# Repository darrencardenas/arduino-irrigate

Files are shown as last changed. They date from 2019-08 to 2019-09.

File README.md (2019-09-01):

# arduino-irrigate

 ## Introduction
 
 This project contains code, schematics, build plans, and [3D models](https://www.thingiverse.com/thing:3825186) to construct an automated garden watering system.  The main components of the system are an [Arduino Uno Rev3 microcontroller board](https://store.arduino.cc/usa/arduino-uno-rev3), a [soil moisture sensor](https://vegetronix.com/Products/VH400/), and a [water solenoid valve](https://www.adafruit.com/product/997).  The water solenoid valve is connected to a garden hose and a suitable watering device, such as a sprinkler or sprayer.  I used an old garden hose with holes drilled into it.  
 
<p align="center">
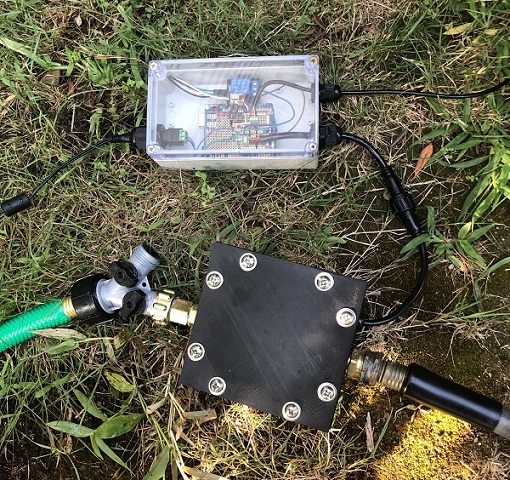
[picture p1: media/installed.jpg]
Installed System

</p>
<p align="center">
Watering Video
</p>   
<br><br>
 
 ## Operation
 At a set time interval, the Arduino checks the moisture sensor for a minimum value. If the reading is below the minimum value, the water valve is opened for a period of time.  The moisture readings are sent via [email](https://www.smtp2go.com/setupguide/arduino/) and [text message](https://www.lifewire.com/sms-gateway-from-email-to-sms-text-message-2495456).  The readings are also saved to a [publicly viewable IoT website](https://community.thingspeak.com/tutorials/arduino/send-data-to-thingspeak-with-arduino/) to store data and generate graphs.

<p align="center">
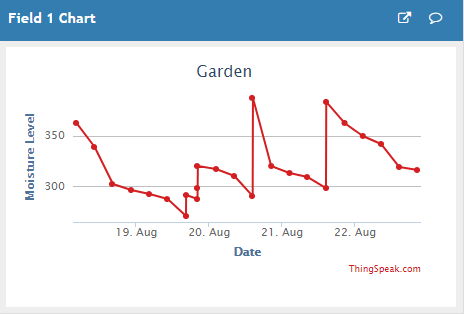
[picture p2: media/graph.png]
Moisture Graph

&nbsp&nbsp&nbsp&nbsp&nbsp&nbsp&nbsp&nbsp&nbsp
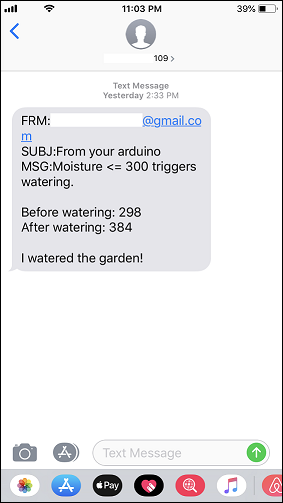
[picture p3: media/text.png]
Text Message

</p>
<br><br>

## Features
- Allows customizable intervals for soil moisture checks and watering
- Leverages waterproof enclosures and cabling
- Sends email and text message (SMS) status updates
- Provides data monitoring via website
- Supports WiFi data transmission using an ESP8266 module
- Powered by a single +12VDC source
<br><br>

<p align="center">
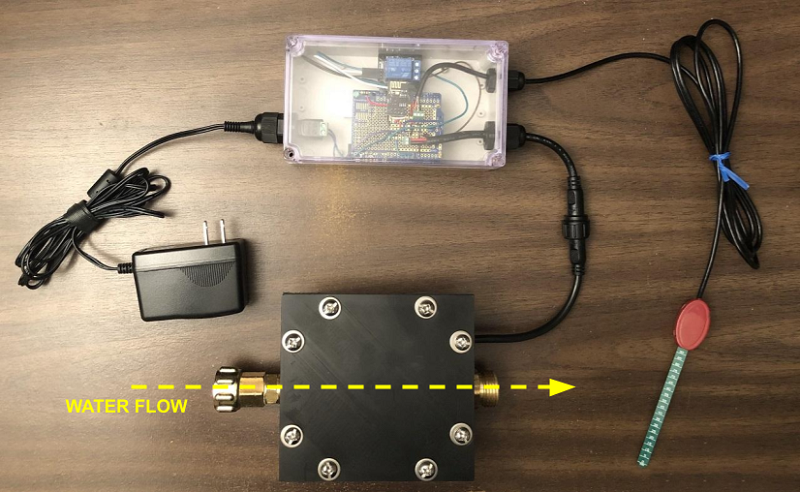
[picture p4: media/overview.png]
Top Down View

</p>
<br><br>

## Schematic Diagram
<p align="center">
<a href="build_plans/schematic_irrigate.pdf">
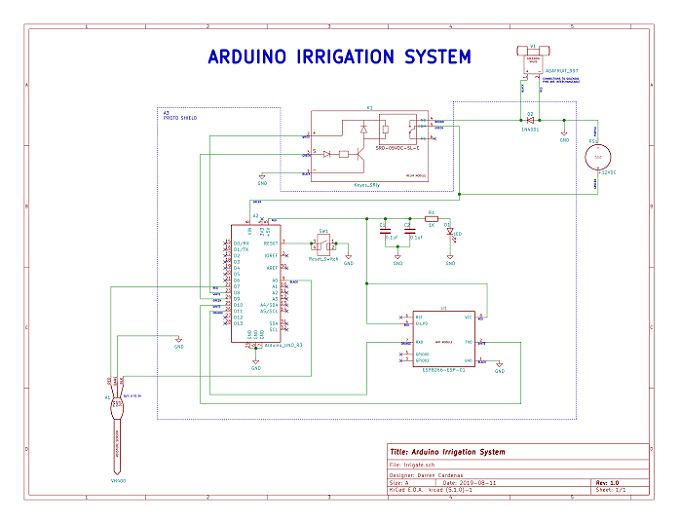
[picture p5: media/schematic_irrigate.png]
</a></p>
<br><br>

## Arduino Code
Developed in Arduino IDE 1.8.9.
<p align="left">
<a href="code/irrigate.ino">
INO file</a></p>
<br><br>

## Arduino Proto Shield Layout
I used screw terminal blocks and a 2x4 female header to allow for easy disassembly.
<p align="center">
<a href="build_plans/shield-layout_irrigate.png">
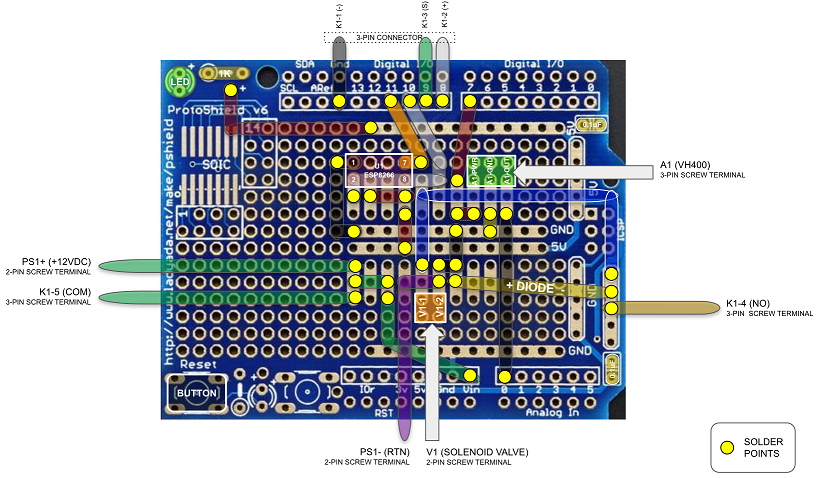
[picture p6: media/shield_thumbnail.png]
</a></p>
<br><br>

## 3D Printed Models
I designed a [custom waterproof enclosure](https://www.thingiverse.com/thing:3825186) to house the water solenoid valve. I used PETG filament and 0.3mm layer height. Enclosure was printed with 10% infill and supports.  Lid was printed with 50% infill and no supports.  I cut a square using gasket material and punched holes for stainless steel screws. 
<p align="center">
<a href="3D_models">
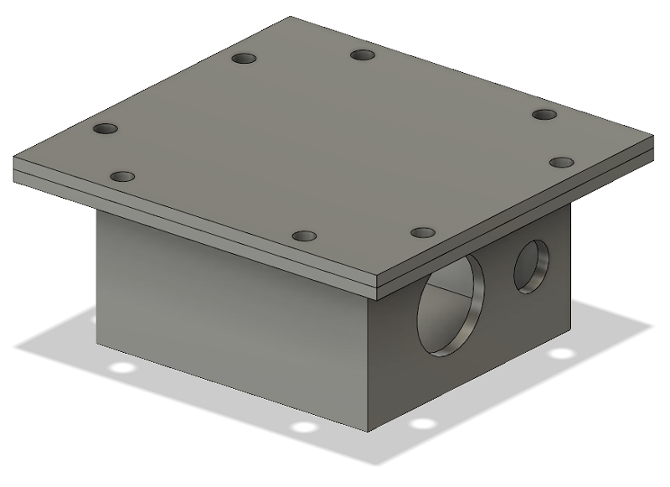
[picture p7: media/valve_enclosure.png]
</a></p>
<br>
<p align="center">
<a href="3D_models/valve_enclosure.stl">
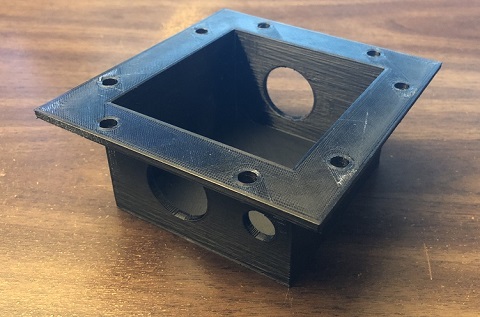
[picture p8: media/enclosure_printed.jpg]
</a>
&nbsp&nbsp
<a href="3D_models/valve_lid.stl">
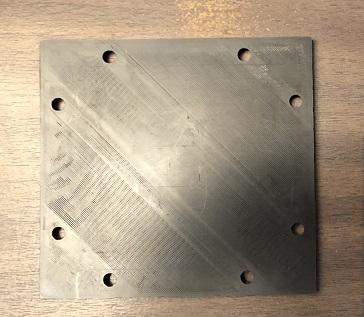
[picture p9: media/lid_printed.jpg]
</a></p>
<br><br>

## Water Solenoid Valve Enclosure 
To install the solenoid valve, insert the bulkhead adapters into the enclosure first.  Then, connect the valve to one of the bulkhead adapters by turning the adapter from outside of the enclosure.  After tightening the first adapter, there should be enough clearance to attach the second adapter.  Then install the bulkhead rubber washers and locknuts. The pipe fittings require teflon tape or thread sealant for leak-proof operation. 
<p align="center">
<a href="build_plans/assembly_valve_enclosure.pdf">
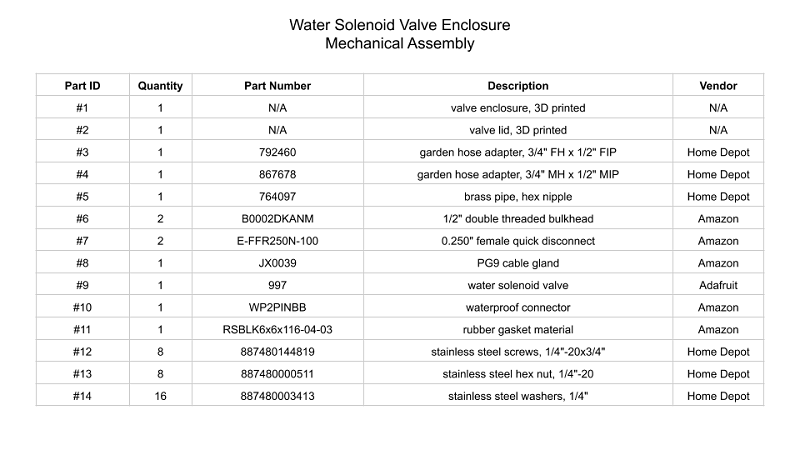
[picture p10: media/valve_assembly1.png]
Valve Assembly 1

</a></p> 
 
<p align="center">
<a href="build_plans/assembly_valve_enclosure.pdf">
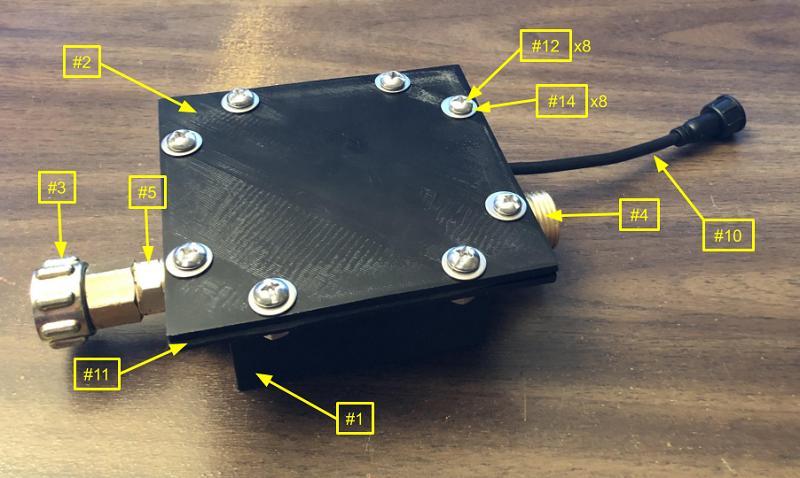
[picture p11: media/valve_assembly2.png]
Valve Assembly 2

</a></p> 

<p align="center">
<a href="build_plans/assembly_valve_enclosure.pdf">
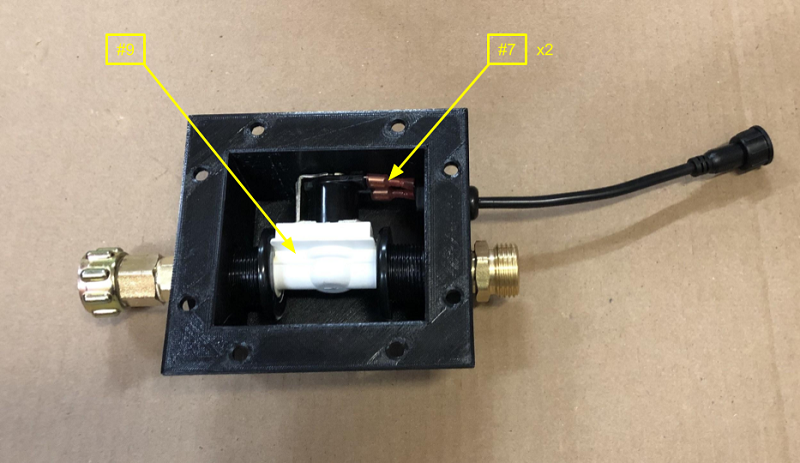
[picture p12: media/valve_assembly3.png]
Valve Assembly 3

</a></p> 

<p align="center">
<a href="build_plans/assembly_valve_enclosure.pdf">
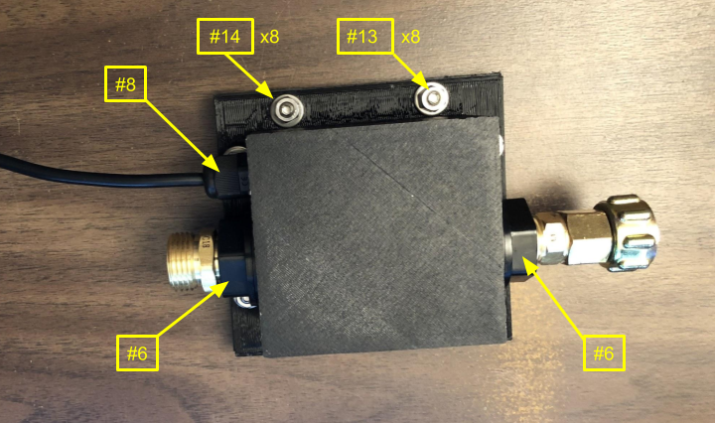
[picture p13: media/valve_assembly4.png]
Valve Assembly 4

</a></p> 
<br><br>

## Arduino Enclosure 
Adafruit provides excellent [instructions](https://learn.adafruit.com/adafruit-proto-shield-arduino?view=all) for the initial set up of the Arduino proto shield.
Install screws and standoffs on the Arduino and relay module. Then use some kind of adhesive to bond the standoffs to the inside of the enclosure.  I used acrylic cement.
<p align="center">
<a href="build_plans/assembly_arduino_enclosure.pdf">
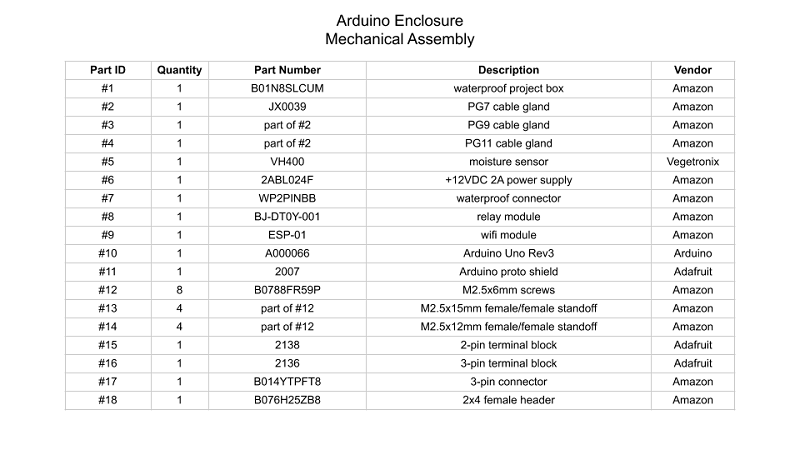
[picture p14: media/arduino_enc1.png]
Arduino Enclosure 1

</a></p> 

<p align="center">
<a href="build_plans/assembly_arduino_enclosure.pdf">
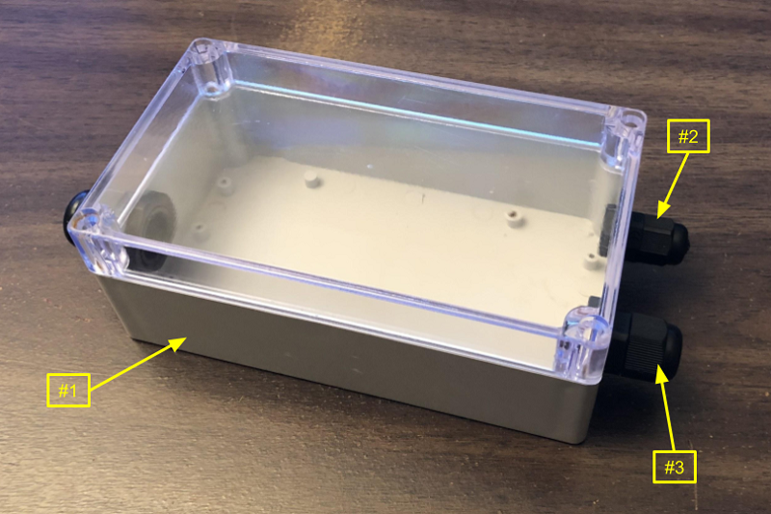
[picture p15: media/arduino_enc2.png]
Arduino Enclosure 2

</a></p> 

<p align="center">
<a href="build_plans/assembly_arduino_enclosure.pdf">
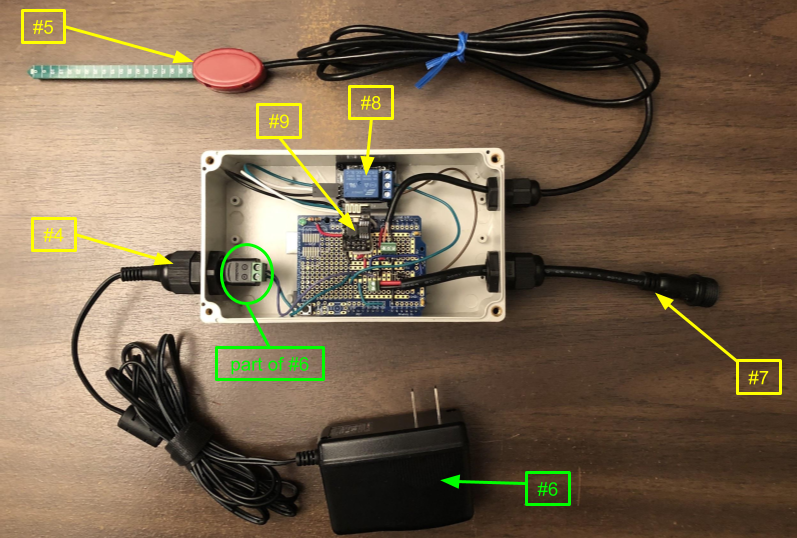
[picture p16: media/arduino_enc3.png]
Arduino Enclosure 3

</a></p> 

<p align="center">
<a href="build_plans/assembly_arduino_enclosure.pdf">
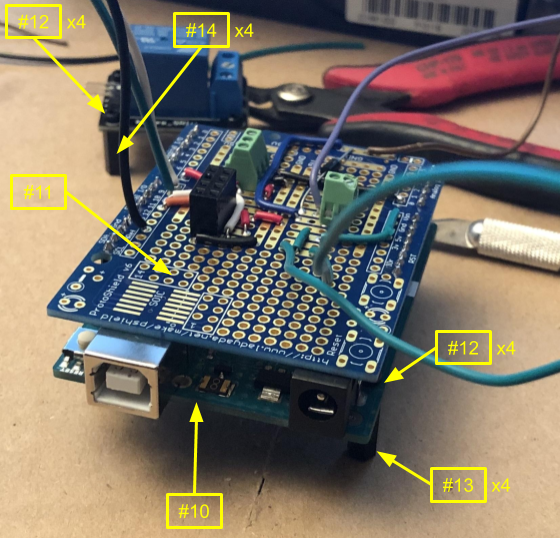
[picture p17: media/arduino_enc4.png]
Arduino Enclosure 4

</a></p> 

<p align="center">
<a href="build_plans/assembly_arduino_enclosure.pdf">
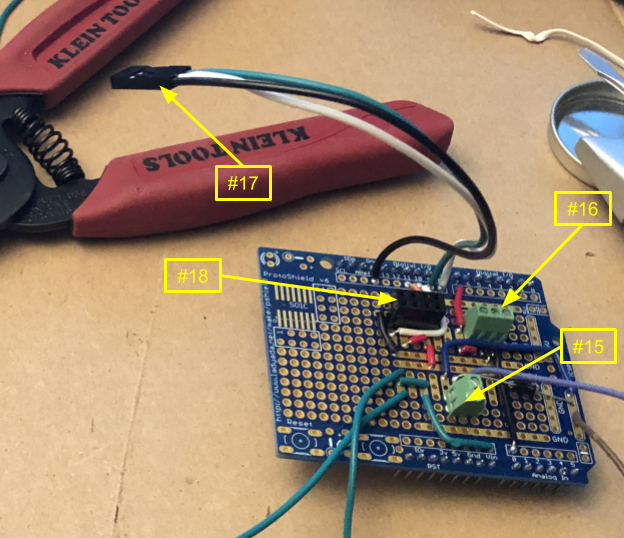
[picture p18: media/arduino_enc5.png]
Arduino Enclosure 5

</a></p> 
<br><br>

## Set Up
- Update the code to include your SSID name/password, [ThingSpeak Write API key](https://community.thingspeak.com/tutorials/arduino/send-data-to-thingspeak-with-arduino/), and [SMTP2GO username/password](https://www.smtp2go.com/setupguide/arduino/).
- Update the email sender and [recipient](https://www.lifewire.com/sms-gateway-from-email-to-sms-text-message-2495456) lists in the code.
- Update the moisture check interval and watering period in the code.
- Update the MOISTURE_MAX value in the code by taking readings with the sensor blade fully submerged in water.
- Update the MOISTURE_THRESHOLD value in the code with your desired value. 
- Ensure water pressure going to the [water solenoid valve](https://www.adafruit.com/product/997) is at least 3PSI.
- The water solenoid valve is uni-directional. Confirm water flow will be in the correct direction.

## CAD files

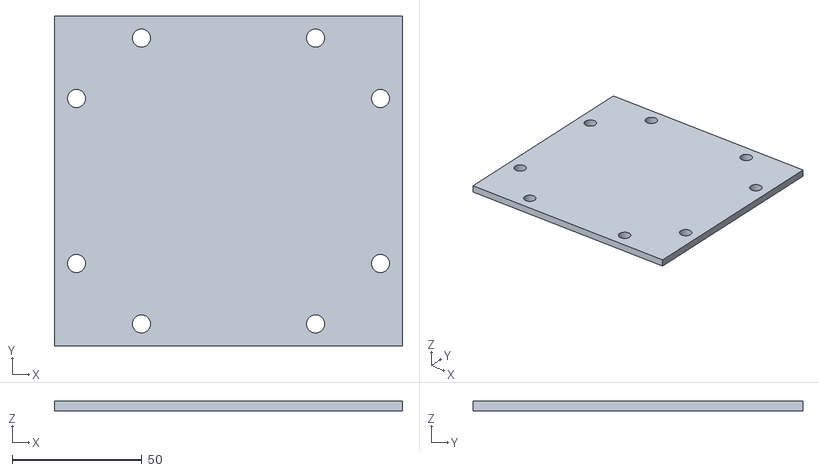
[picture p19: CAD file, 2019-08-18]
3D_models/valve_lid.stl
134.0 x 127.0 x 4.00

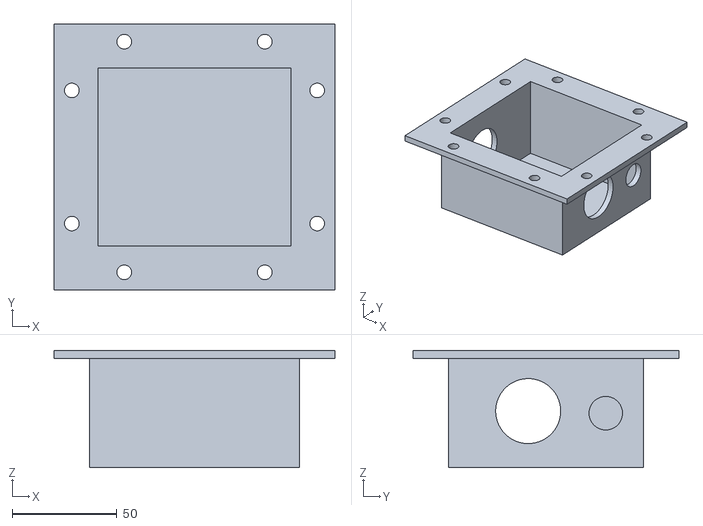
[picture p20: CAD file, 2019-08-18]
3D_models/valve_enclosure.stl
134.0 x 127.0 x 56.0

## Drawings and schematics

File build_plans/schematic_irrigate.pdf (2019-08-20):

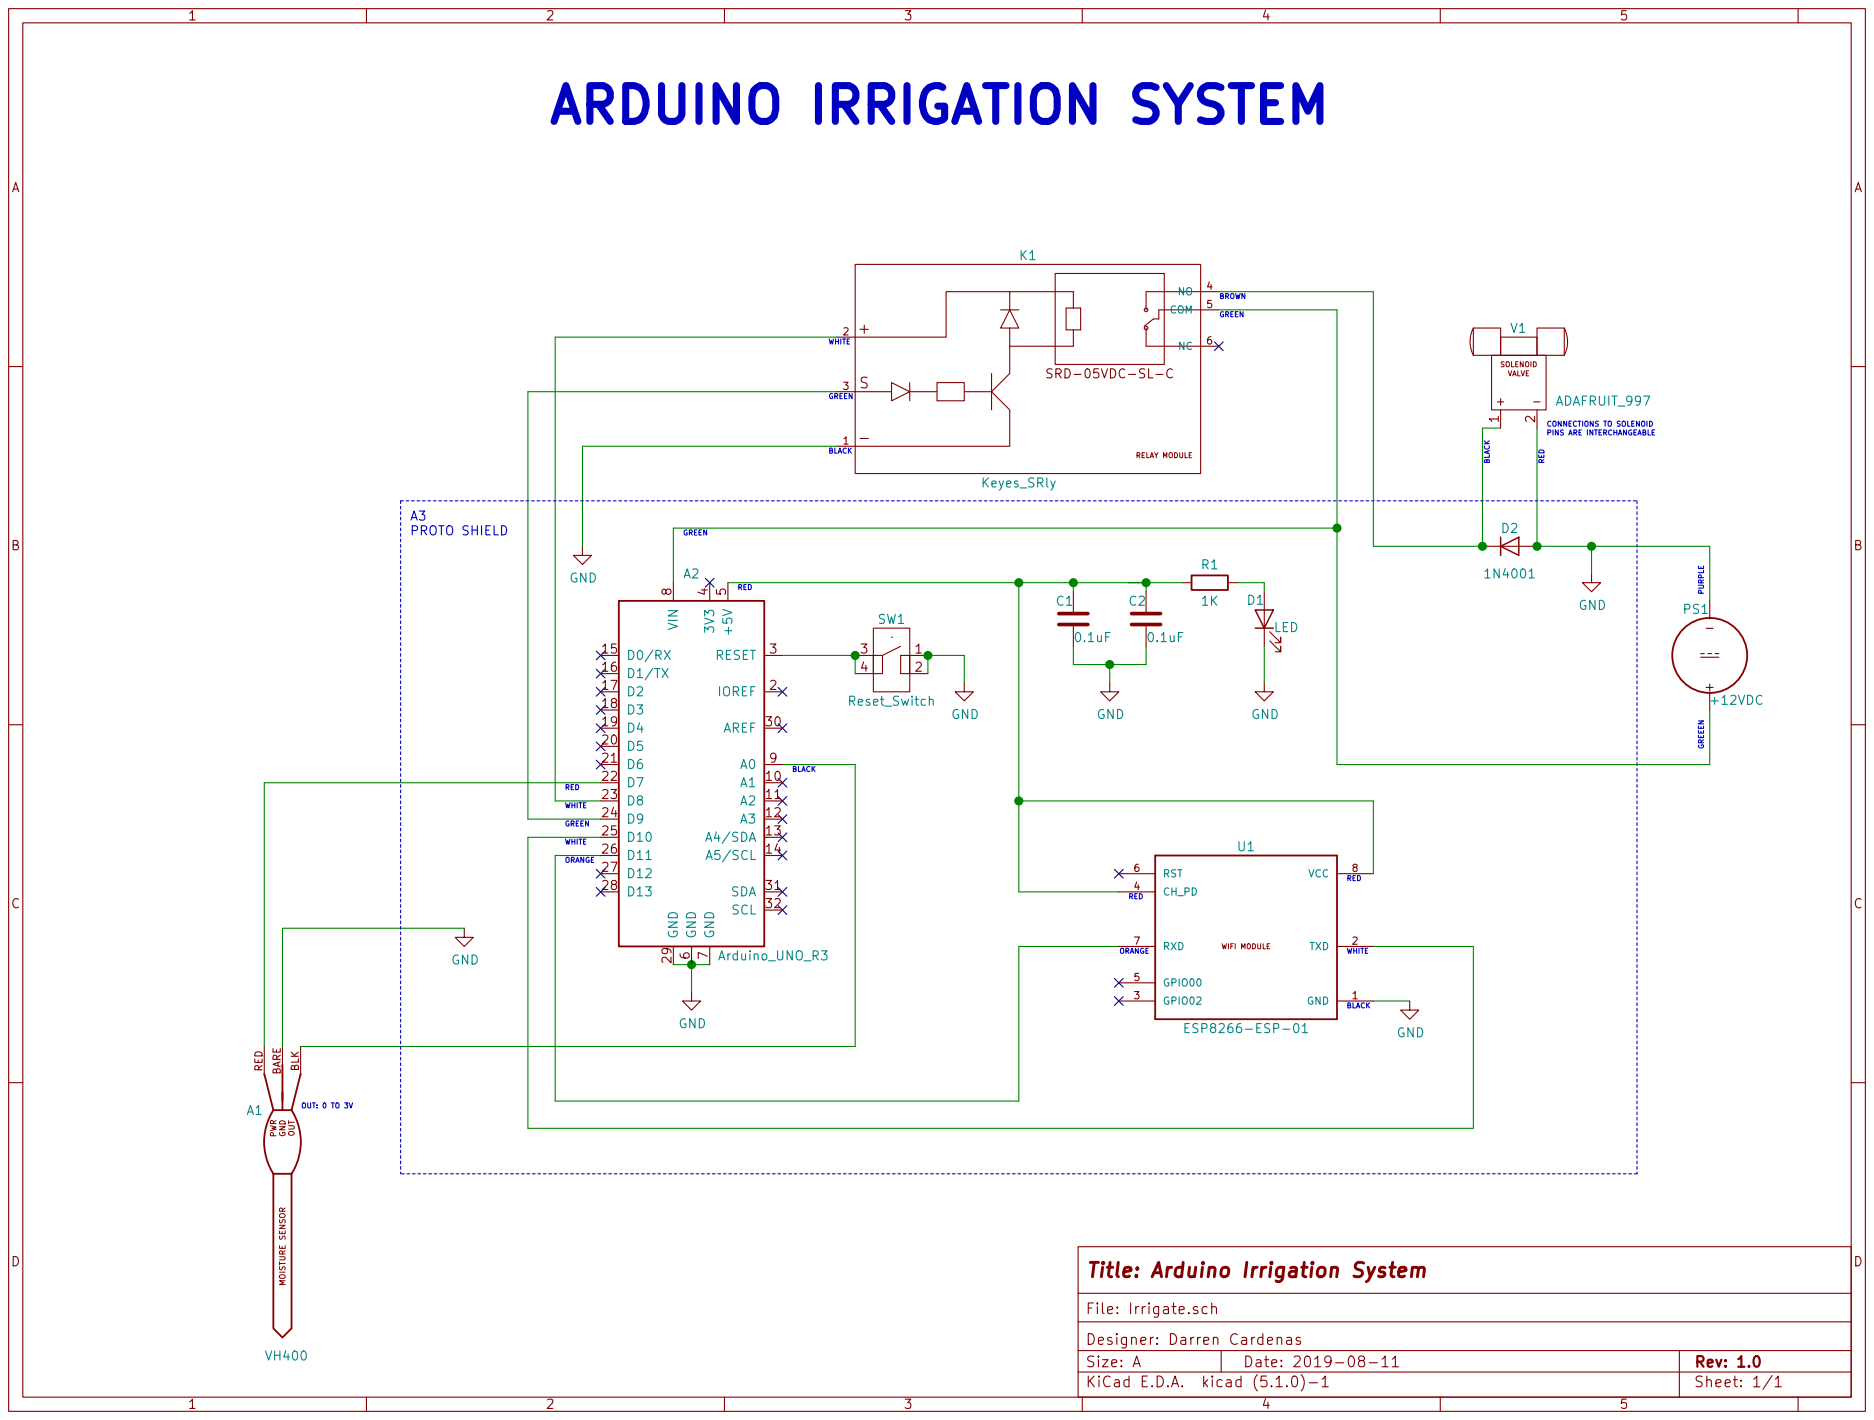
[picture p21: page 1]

PINS ARE INTERCHANGEABLE GND

8 A0 9 A2 Arduino_UNO_R3 PWR GND MOISTURE SENSOR OUT BARE RED BLK A1 VH400

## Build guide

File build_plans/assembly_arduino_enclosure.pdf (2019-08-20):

Part ID | Quantity | Part Number | Description | Vendor
#1 | 1 | B01N8SLCUM | waterproof project box | Amazon

#2 | 1 | JX0039 | PG7 cable gland | Amazon

#3 | 1 | part of #2 | PG9 cable gland | Amazon

#4 | 1 | part of #2 | PG11 cable gland | Amazon

#5 | 1 | VH400 | moisture sensor | Vegetronix

#6 | 1 | 2ABL024F | +12VDC 2A power supply | Amazon

#7 | 1 | WP2PINBB | waterproof connector | Amazon

#8 | 1 | BJ-DT0Y-001 | relay module | Amazon

#9 | 1 | ESP-01 | wifi module | Amazon

#10 | 1 | A000066 | Arduino Uno Rev3 | Arduino

#11 | 1 | 2007 | Arduino proto shield | Adafruit

#12 | 8 | B0788FR59P | M2.5x6mm screws | Amazon

#13 | 4 | part of #12 | M2.5x15mm female/female standoff | Amazon

#14 | 4 | part of #12 | M2.5x12mm female/female standoff | Amazon

#15 | 1 | 2138 | 2-pin terminal block | Adafruit

#16 | 1 | 2136 | 3-pin terminal block | Adafruit

#17 | 1 | B014YTPFT8 | 3-pin connector | Amazon

#18 | 1 | B076H25ZB8 | 2x4 female header | Amazon

## Arduino Enclosure Mechanical Assembly

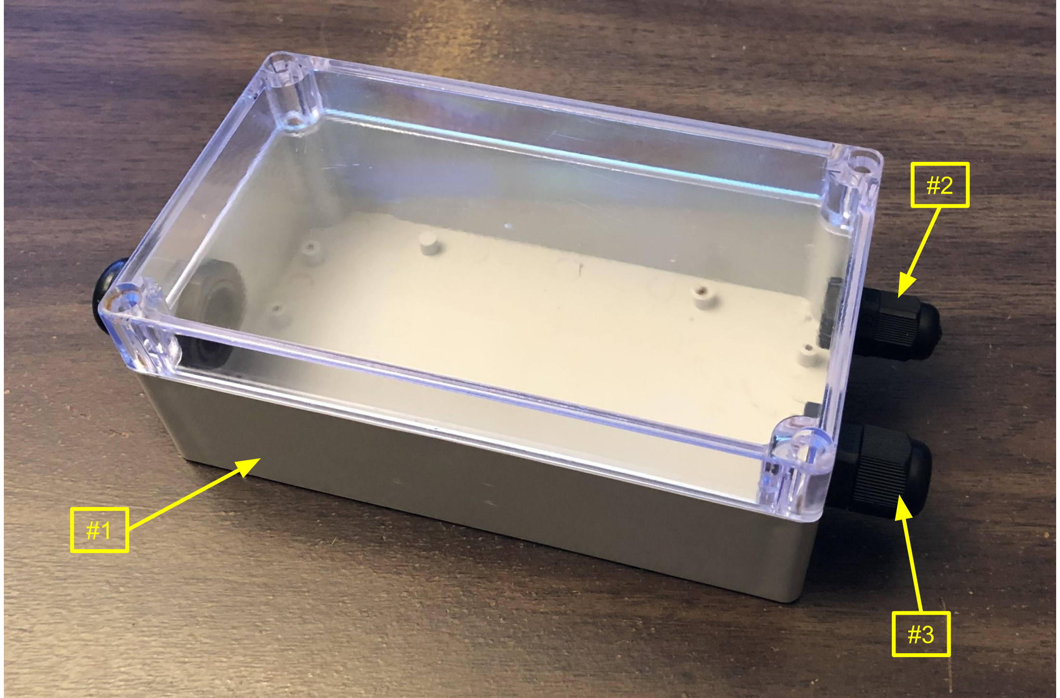
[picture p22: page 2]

#1

#2

#3

#5

#8

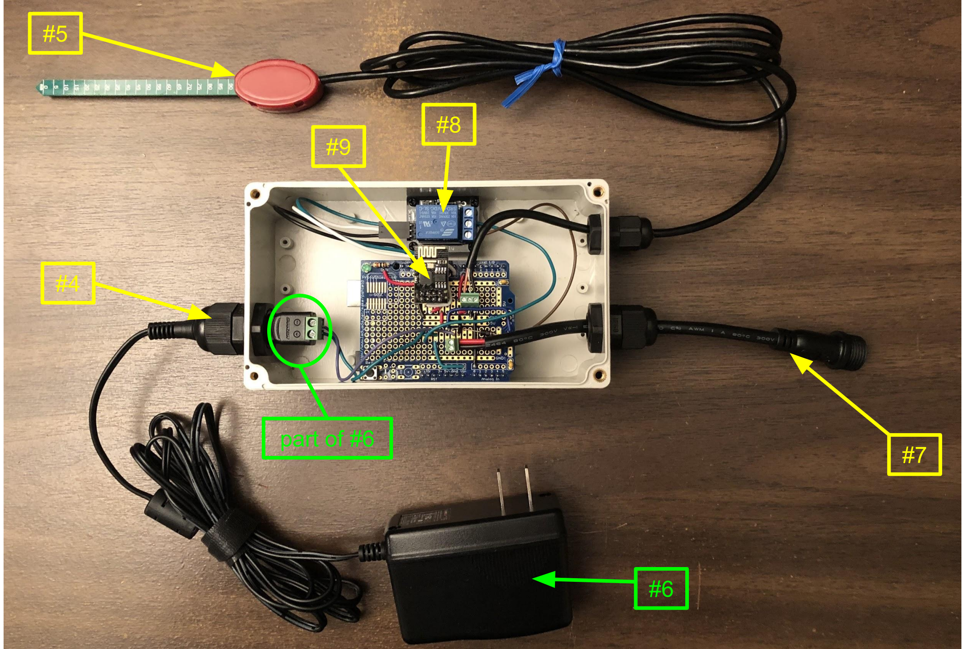
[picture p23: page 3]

#6

#4

## #7 part of #6

#9

#12 | x4 | #14 | x4

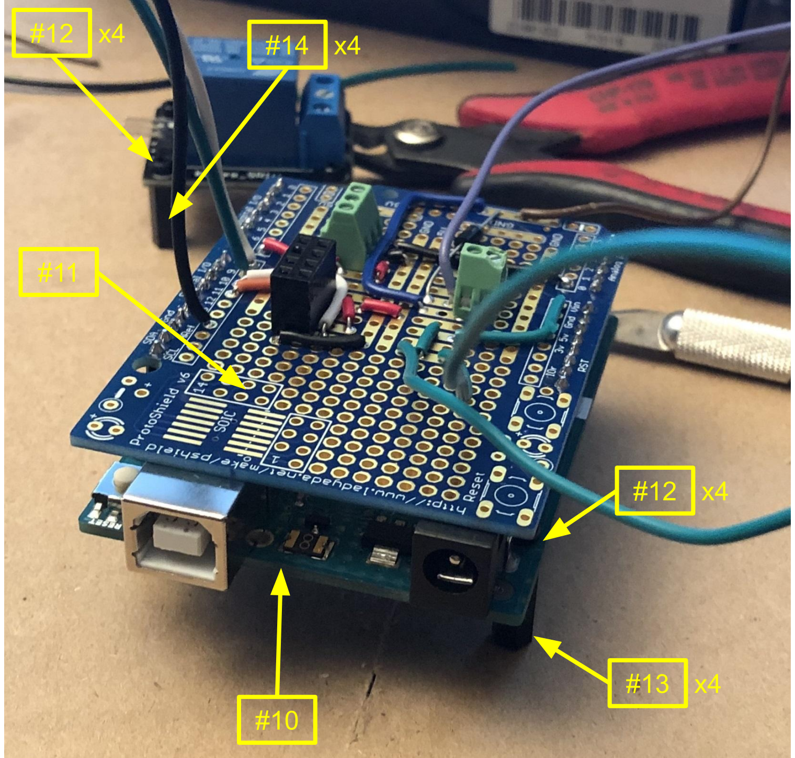
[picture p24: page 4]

#11

#10

#12 | x4

#13 | x4

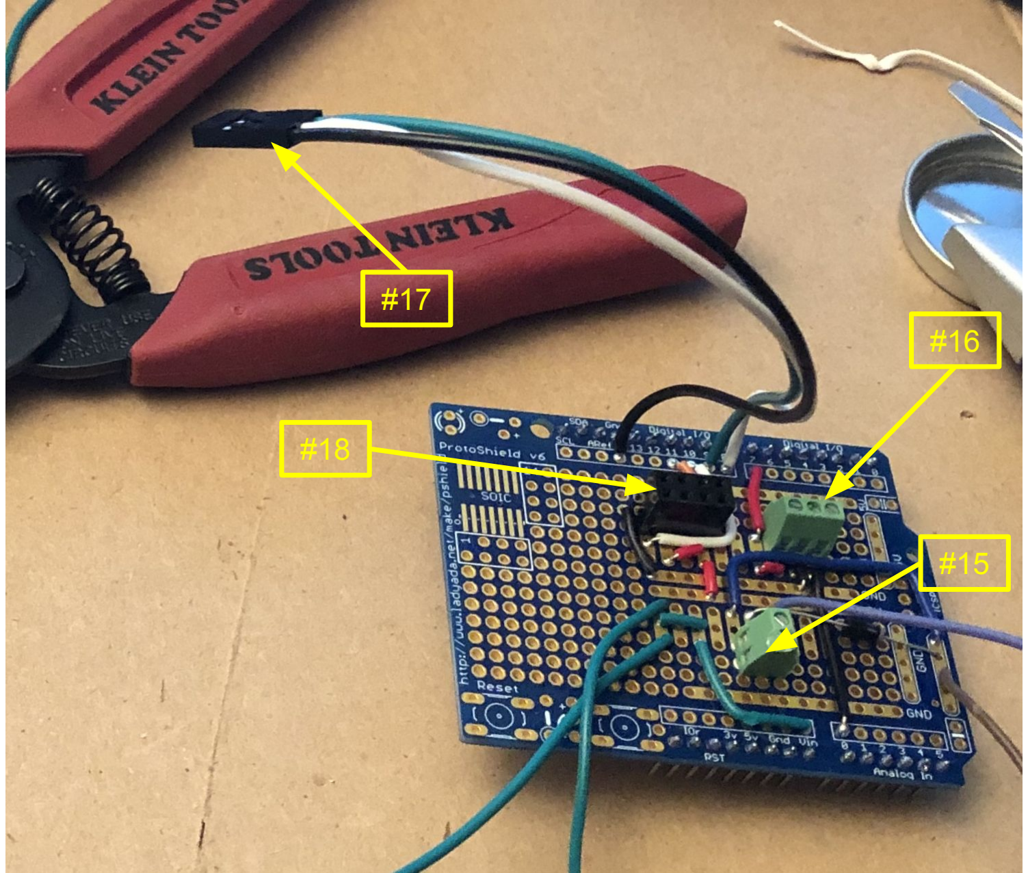
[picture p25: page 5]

#17

#18

#15

#16

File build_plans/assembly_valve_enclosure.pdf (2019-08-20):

## Water Solenoid Valve Enclosure Mechanical Assembly

Part ID | Quantity | Part Number | Description | Vendor
#1 | 1 | N/A | valve enclosure, 3D printed | N/A

#2 | 1 | N/A | valve lid, 3D printed | N/A

#3 | 1 | 792460 | garden hose adapter, 3/4" FH x 1/2" FIP | Home Depot

#4 | 1 | 867678 | garden hose adapter, 3/4" MH x 1/2" MIP | Home Depot

#5 | 1 | 764097 | brass pipe, hex nipple | Home Depot

#6 | 2 | B0002DKANM | 1/2" double threaded bulkhead | Amazon

#7 | 2 | E-FFR250N-100 | 0.250" female quick disconnect | Amazon

#8 | 1 | JX0039 | PG9 cable gland | Amazon

#9 | 1 | 997 | water solenoid valve | Adafruit

#10 | 1 | WP2PINBB | waterproof connector | Amazon

#11 | 1 | RSBLK6x6x116-04-03 | rubber gasket material | Amazon

#12 | 8 | 887480144819 | stainless steel screws, 1/4"-20x3/4" | Home Depot

#13 | 8 | 887480000511 | stainless steel hex nut, 1/4"-20 | Home Depot

#14 | 16 | 887480003413 | stainless steel washers, 1/4" | Home Depot

#2

#12

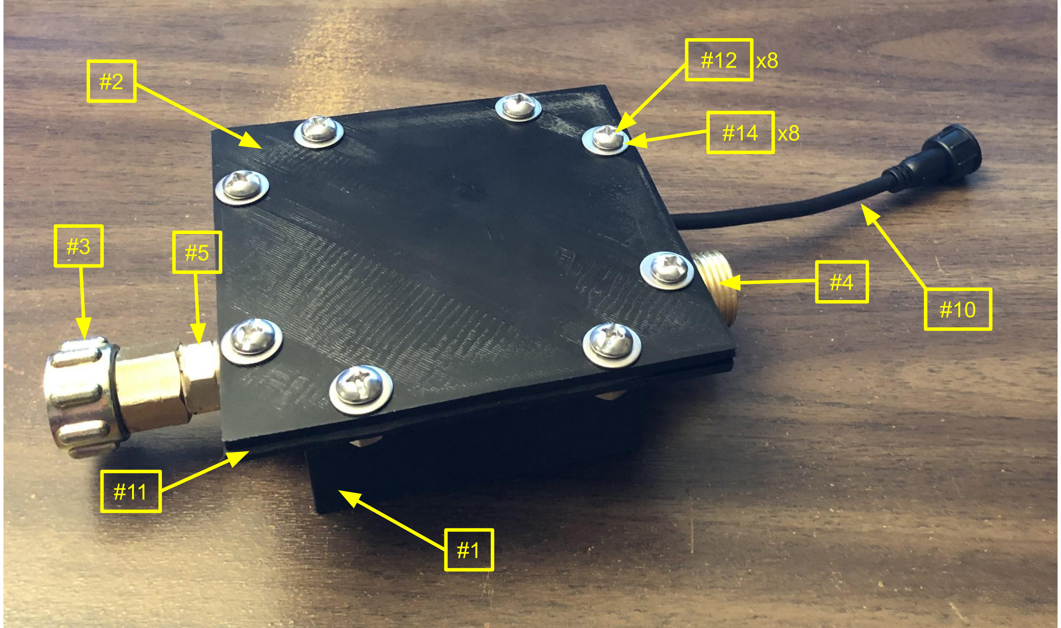
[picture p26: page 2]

#4

#10

#11

x8

#3 | #5

#1

#14 x8

#9 | #7 | x2

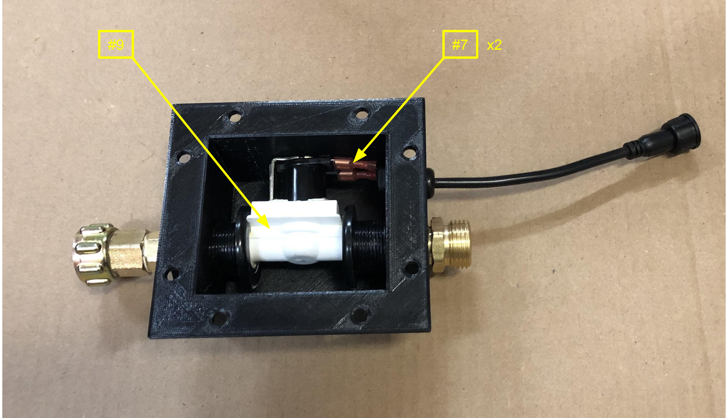
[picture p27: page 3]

#8

#14 | #13

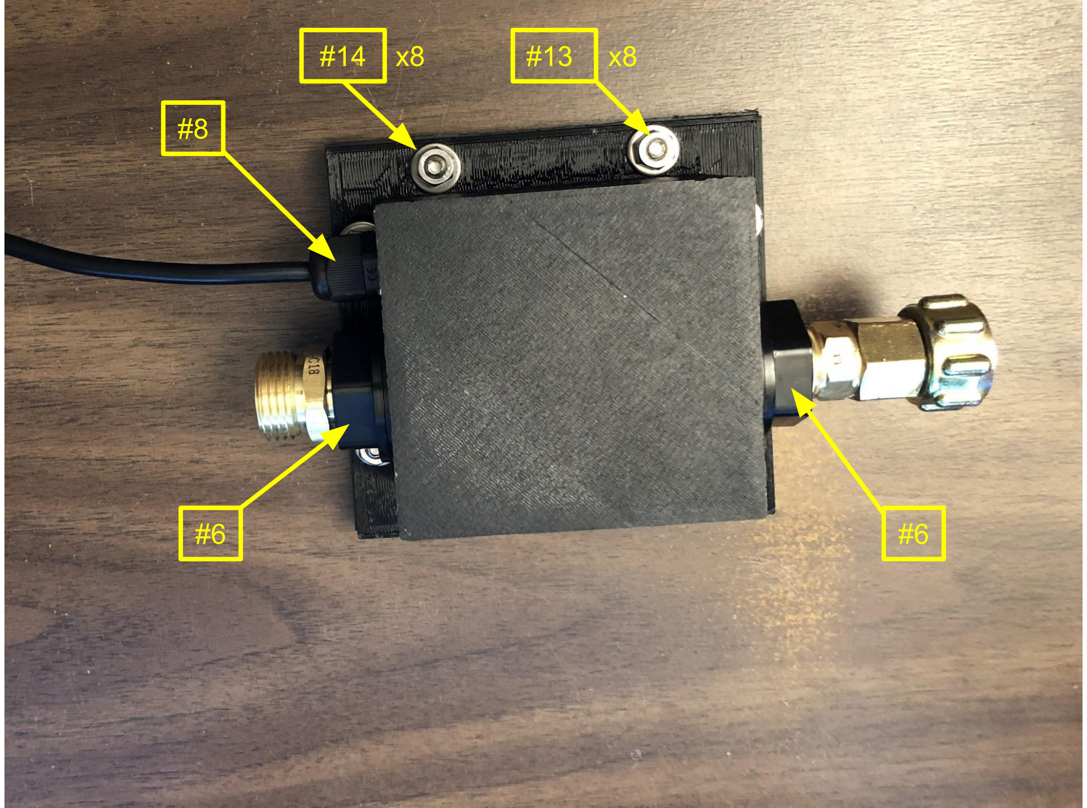
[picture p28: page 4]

#6

#6

x8 | x8

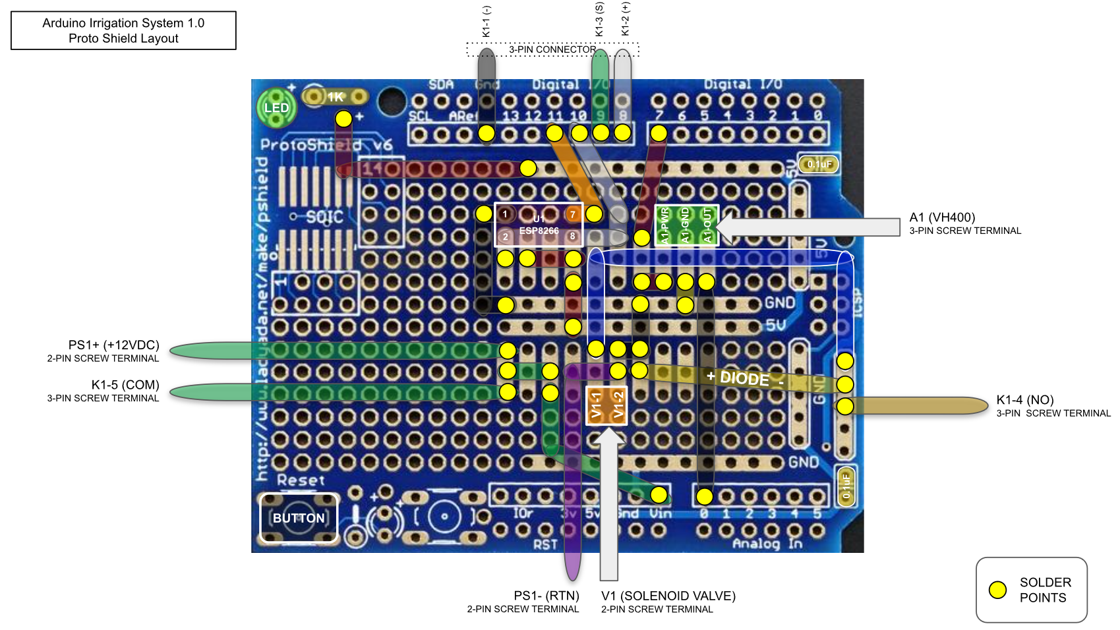
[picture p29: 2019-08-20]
build_plans/shield-layout_irrigate.png

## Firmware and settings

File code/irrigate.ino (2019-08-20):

/*
 * Title:  Arduino Irrigation System 
 *
 * Version: 1.0
 * 
 * Author: Darren Cardenas
 * 
 * Date:   11 August 2019
 * 
 * Description: This program checks a moisture sensor for a minimum value. If the value is
 *              below the minimum, a water valve is opened for a period of time.  The 
 *              moisture readings are sent via email and text message.  The readings are also
 *              saved to a publicly viewable IoT website to store data and generate graphs.
 * 
 */

#include <SoftwareSerial.h>

#define AP_SSID             "SSID_NAME"          // Replace with your wifi SSID name
#define AP_PASSWORD         "SSID_PASSWORD"      // Replace with your wifi SSID password

#define IOT_WEBSITE         "api.thingspeak.com"
#define IOT_PORT            80
#define IOT_KEY             "ABCDEFGHIJKLMNOP"   // Replace with your ThingSpeak "Write API" key

#define SMTP_SERVER         "mail.smtp2go.com"
#define SMTP_PORT           2525
#define SMTP_USERNAME       "abcdefghijklmnopqrstuv0123456789"  // Replace with your SMTP2GO Base64-encoded username
#define SMTP_PASSWORD       "zyxwvutsrqponmlkjihgfe9876543210"  // Replace with your SMTP2GO Base64-encoded password

#define EMAIL_ADDR_SENDER   "your@email.com"         // Replace with sender email address
    
const char *RECIPIENTS[] = {
                            "your@email.com",        // Replace with recipient email address
                            "5551234567@vtext.com",  // Replace with mobile number email address (for SMS/text message)
                           };

const int NUM_RECIPIENTS = sizeof(RECIPIENTS) / sizeof(RECIPIENTS[0]);

// How often to check moisture
#define STATUS_CHECK_HRS          6 // Hours

// How long to allow the water valve to stay open
#define WATERING_PERIOD_MINS      5 // Minutes

// Moisture sensor maximum value
#define MOISTURE_MAX         640   // Take reading with moisture sensor blade fully submerged in water

// A moisture value less than or equal to this triggers watering
#define MOISTURE_THRESHOLD   300   // Modify with desired threshold

// Pin definitions
#define VALVE_RELAY_SIG  8  // Controls the valve
#define VALVE_RELAY_VCC  9  // Powers the relay
#define RX              10  // Receives from the wifi module
#define TX              11  // Transmits to the wifi module
#define MOISTURE_VCC     7  // Powers the moisture sensor
#define MOISTURE_SENSOR  0  // Analog, reads from the moisture sensor

// Delay values
#define RELAY_DELAY           500   // milliseconds
#define MOISTURE_DELAY        1000  // milliseconds
#define WIFI_CMD_DELAY        1000  // milliseconds
#define WIFI_CMD_LONG_DELAY   4000  // milliseconds

// Baud rates
#define BAUD_SERIAL    9600
#define BAUD_WIFI    115200


SoftwareSerial esp8266(RX,TX);


//-------------------------
// Arduino Functions
//-------------------------


// This function runs once at power-on or reset
void setup()
{   
  pinMode(VALVE_RELAY_VCC, OUTPUT);  // Powers the relay
  pinMode(VALVE_RELAY_SIG, OUTPUT);  // Controls the valve
  pinMode(MOISTURE_VCC, OUTPUT);     // Powers the moisture sensor

  Serial.begin(BAUD_SERIAL);         // Use Serial Monitor for debug statements
  Serial.println("Sketch started");  
  
  setupComm();
}


// This function runs after setup() and repeats forever
void loop()
{  
  int moisture_val_init = 0;   // Moisture value before watering
  int moisture_val_end = 0;    // Moisture value after watering

  String msg = "";             // String for email body
  
  // Get the moisture reading
  Serial.println("Checking moisture ...");
  moisture_val_init = getMoistureVal();
  Serial.println(String("Moisture value: ") + moisture_val_init);

  // Update channel feed with moisture level  
  updateChannelFeed(moisture_val_init);

  // Soil is too dry
  if (moisture_val_init <= MOISTURE_THRESHOLD)
  {
    unsigned long watering_time = WATERING_PERIOD_MINS*60000;  // Convert minutes to milliseconds   
    Serial.println(String("Soil is too dry. Watering for ") + WATERING_PERIOD_MINS + String(WATERING_PERIOD_MINS == 1 ? " minute." : " minutes."));

    digitalWrite(VALVE_RELAY_VCC, HIGH);  //  Apply power to water valve relay
    delay(RELAY_DELAY);
    digitalWrite(VALVE_RELAY_SIG, HIGH);  // Turn on water valve
    
    // Leave water valve open for a set amount of time
    delay(watering_time);  

    // Close water valve
    digitalWrite(VALVE_RELAY_SIG, LOW); 
    delay(RELAY_DELAY);
    digitalWrite(VALVE_RELAY_VCC, LOW);
     
    Serial.println("Watering is complete.");
    
    // Get the moisture reading after watering
    Serial.println("Checking moisture after watering ...");
    moisture_val_end = getMoistureVal();
    Serial.println(String("Moisture value after watering: ") + moisture_val_end);
    
    // Update channel feed with moisture level  
    updateChannelFeed(moisture_val_end);

    // Send status email
    msg = String("Moisture <= ") + MOISTURE_THRESHOLD + String(" triggers watering.\n\n") + 
          String("Before watering: ") + moisture_val_init + String("\n") +
          String("After watering: ") + moisture_val_end + String("\n\n") + 
          String("I watered the garden!");
    Serial.println(msg);
    sendEmail(msg);
  }
  // Soil moisture is good
  else
  {
    // Send status email
    msg = String("Moisture <= ") + MOISTURE_THRESHOLD + String(" triggers watering.\n\n") + 
          String("Moisture value: ") + moisture_val_init + String("\n\n") +
          String("The garden does not need watering!");
    Serial.println(msg);
    sendEmail(msg);            
  }

  // Wait for next status check
  unsigned long wait_time = STATUS_CHECK_HRS*3600000;   // Convert hours to milliseconds
  Serial.print(String("Waiting for ") + STATUS_CHECK_HRS + String(STATUS_CHECK_HRS == 1 ? " hour" : " hours") + String(" before checking again.\n"));
  delay(wait_time); 
  
}  // End of loop()


//-------------------------
// Utility Functions
//-------------------------

// This function gets a moisture value
int getMoistureVal (void)
{
  int val = 0;
  
  digitalWrite(MOISTURE_VCC, HIGH);   // Apply power to moisture sensor
  delay(MOISTURE_DELAY);              // Wait for stable output
  val = analogRead(MOISTURE_SENSOR);  // Read the moisture sensor
  digitalWrite(MOISTURE_VCC, LOW);    // Turn off to prolong life of sensor
  
  return val;
  
}  // End of getMoistureVal()


// Send email with username and password encoded in Base64
int sendEmail (String text)
{
  int i = 0;  // Loop iterator
  
  Serial.println("Connecting to SMTP server ...");
  esp8266.println(String("AT+CIPSTART=2,\"TCP\",\"") + String(SMTP_SERVER) + String("\",") + SMTP_PORT);
  delay(WIFI_CMD_LONG_DELAY);

  // Send commands to SMTP server
  Serial.println("Sending commands to SMTP server ...");
  Serial.println("EHLO arduino");
  sendWifiCmd("EHLO arduino");  
  Serial.println("AUTH LOGIN");
  sendWifiCmd("AUTH LOGIN");  
  Serial.println("Username");
  sendWifiCmd(SMTP_USERNAME);  
  Serial.println("Password");
  sendWifiCmd(SMTP_PASSWORD);    
  Serial.println("MAIL FROM");
  sendWifiCmd(String("MAIL FROM:<") + String(EMAIL_ADDR_SENDER) + String(">"));      
  Serial.println("RCPT TO");

  // Loop through all email recipients
  for (i=0; i<NUM_RECIPIENTS; i++)
  {
    Serial.println(String("Emailing ") + String(RECIPIENTS[i]));
    sendWifiCmd(String("RCPT TO:<") + String(RECIPIENTS[i]) + String(">"));
  }
  // End loop through all email recipients
  
  Serial.println("DATA");
  Serial.println(text);
  sendWifiCmd("DATA");
  sendWifiCmd(String("from: ") + String(EMAIL_ADDR_SENDER));
  sendWifiCmd("SUBJECT: From your arduino");  // Do not edit
  sendWifiCmd("");
  sendWifiCmd(text);
  sendWifiCmd(".");
  sendWifiCmd("QUIT");
  Serial.println("DONE");
  return 0;
  
}  // End of sendEmail()


// This function sends a command to the wifi module
int sendWifiCmd (String cmd)
{
  esp8266.println("AT+CIPSEND=2," + String(cmd.length()+2));
  delay(WIFI_CMD_DELAY);  
  esp8266.println(cmd);
  delay(WIFI_CMD_DELAY);  
  return 0;
  
}  // End of sendWifiCmd()


// This function sets up communications
void setupComm (void)
{
  esp8266.begin(BAUD_WIFI);  
  
  // Set WiFi mode 
  esp8266.println("AT+CWMODE=1");  

  Serial.print("Connecting to wifi ...");

  // Join access point
  esp8266.println(String("AT+CWJAP=\"") + String(AP_SSID) + String("\",\"") + String(AP_PASSWORD) + String("\""));  
  delay(WIFI_CMD_LONG_DELAY*3);  // Handle potentially slow router responses

  // Allow multiple TCP connections
  esp8266.println("AT+CIPMUX=1");
  delay(WIFI_CMD_LONG_DELAY*2);  // Handle potentially slow router responses
  
  Serial.println("Done");
  
}  // End of setupComm()


// This function updates an IoT channel with a value
void updateChannelFeed (int value)
{
    Serial.print("Updating IoT feed ... ");

    // Connect to IoT server
    esp8266.println(String("AT+CIPSTART=0,\"TCP\",\"") + String(IOT_WEBSITE) + String("\",") + String(IOT_PORT));
    delay(WIFI_CMD_LONG_DELAY);
    String url = String("GET /update?api_key=") + String(IOT_KEY) + String("&field1=") + value; 

    // Send data to IoT server
    esp8266.println("AT+CIPSEND=0," + String(url.length()+2));
    delay(WIFI_CMD_LONG_DELAY);
    long bytes_written = esp8266.println(url);

    // Close connection
    esp8266.println("AT+CIPCLOSE=0");
    Serial.println("Done");
    
}  // End of updateChannelFeed()

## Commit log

2019-08-18 Add 3D models for valve enclosure.
    [valve_enclosure.stl, valve_lid.stl]
2019-08-23 Add schematic_irrigate.png
2019-08-23 Remove vertical bar from schematic_irrigate.png
2019-08-23 Add lower case extension for image file
2019-08-23 Add arduino proto shield thumbnail for readme
2019-08-23 Add valve_enclosure.png
2019-08-23 Add 3D printed photos
2019-08-23 Decrease dimensions of 3D printed photos
2019-08-23 Add valve assembly pics
2019-08-23 Add arduino enclosure pics for readme
2019-08-23 Show water flow direction in overview.png
